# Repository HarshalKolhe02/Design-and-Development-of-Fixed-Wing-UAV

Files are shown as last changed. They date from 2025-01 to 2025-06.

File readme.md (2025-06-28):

# DESIGN AND DEVELOPMENT OF FIXED WING UAV
This is official repository of design and development of fixed wing UAV project at IvLabs, VNIT Nagpur
#
<details>
  <summary>Table of Content</summary>
  <ol>
    <li><a href="#DESIGN METHODOGOLGY">Design Methodology</a></li>
   <ol>
     <li><a href="#AIRFOIL SELECTION">Airfoil Selection</a></li>
     <li><a href="#WEIGHT ESTIMATION">Weight Estimation</a></li>
     <li><a href="#Thrust To Weight Ratio">Thrust To Weight Ratio</a></li>
     <li><a href="#Configuration of Aircraft">Configuration of Aircraft</a></li>
     <li><a href="#Estimation and Adjustment">CoG Estimation and Adjustment</a></li>
     <li><a href="#Demensions of Aircraft">Demensions of Aircraft</a></li>
   </ol>   
    <li><a href="#Fabrication">Fabrication</a></li>
     <li><a href=""#Flight Test"">Flight Test</a></li>
  </ol>
</details>

## DESIGN METHODOGOLGY
### AIRFOIL SELECTION
Airfoil selection is done by selecting different airfoils and then analysing them using XFLR5. We found that NACA2412 with camber 4%  gives us $C_l=1$ at 4 $^\circ$ -5 $^\circ$ AOA. The simulation graphs are shown below.

simulation sheet

We have designed rectangular wing using this airfoil and elevator, rudder are kept Flat.

### WEIGHT ESTIMATION
For estimation of weight, we have found weight of each component individually and then added to get final weight of plane. 
The estimated weight was found to be 1580 grams. The actual weight of plane (as of now) is 1350 grams.
### WING SPAN CALCULATION
For the calculation of wing span We have taken aspect ratio to be 5 which is common for trainers UAV. Then by using the relation of wing loading we found that the wing area to be 3125 $cm^2$ 
By using the aspect ratio relation we found the length of wing to be 1.25m and  chord length of 25 cm.

### THRUST TO WEIGHT RATIO
Generally the thrust to weight ratio for a fixed wing plane is kept between $0.5$ to $0.7$ . For this plane we have consider the thrust to weight ratio to be $0.5$ . A thrust-to-weight ratio (TWR) of 0.5 means that the thrust generated by the propulsion system is half the weight of the aircraft.
### CONFIGURATION OF AIRCRAFT
Considering the easy of manufacturing, We have considered the following configuration parameters for the plane
1. High wing configuration with no dihedral
2. Rectangular wing design
3. Tractor configuration
### CoG ESTIMATION AND ADJUSTMENT
The estimation of centre of gravity is done manually using the fact that the weight of the plane is balanced on the centre of gravity. For adjustment of CoG we adjusted the position of the battery to get the Cog behind the aerodynamic centre of plane i.e $\frac{MAC}{4}$.
### Landing gears
We have used a  taildragger configuration of landing gear. The back landing gear is smaller allowing plane’s wing to get required angle of attack during takeoff.
### DIMENSIONS OF AIRCRAFT 
The dimensions of aircraft are calculated using the standard equations of Fixed Wing Aeroplanes and are verified using the calculator Provided by rcplanes.online . 

A CAD model of aircraft is prepared using this dimensions and fabrication is made with refrence to CAD model.

### CAD MODEL

plane alternate

## 
## FABRICATION

The fuselag of plane is made using foam sheet cutted into various pieces and then glued together. The wings are made by using styrofoam blocks from which airfoils are made using hot wire cutter in various parts all these parts are combined using Carbon Fibre Rod. The Elevator, Ailerons and Rudder are made using foam sheet. Servos are used to move the control surfaces. The mount for motor, servo connections and landing gears are 3d printed. The Final Fabricated Plane is shown below.

Final_plane)
##

## FLIGHT TEST

[FLIGHT TEST](https://github.com/user-attachments/assets/4fe1304d-87b4-4691-89f3-da415da7d665)

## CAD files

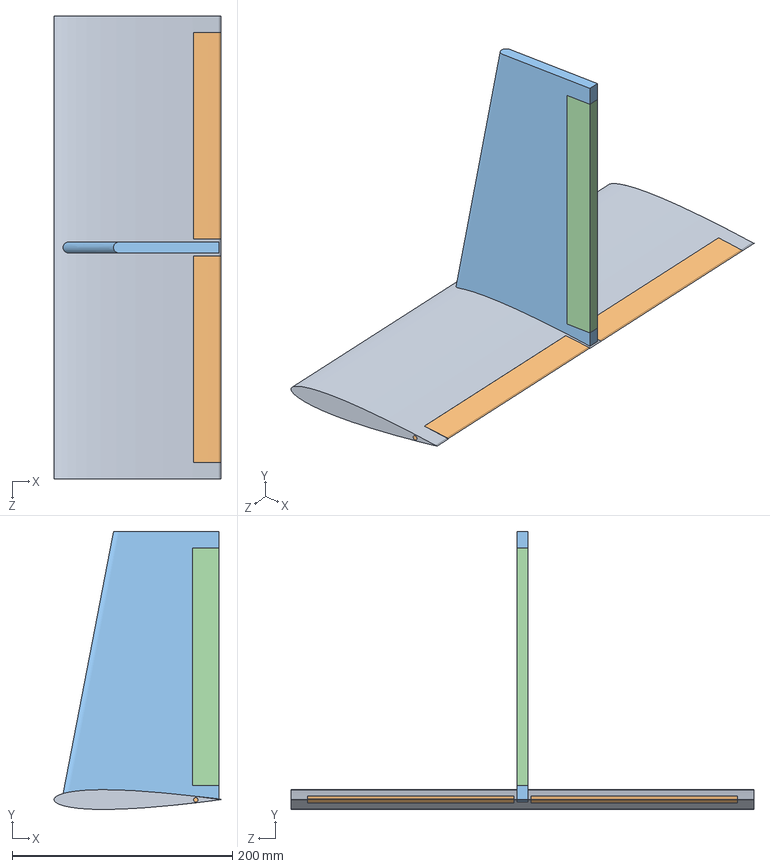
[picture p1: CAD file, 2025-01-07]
CAD files/HS_final.SLDASM
151.3 x 252.2 x 420.0 mm
HS
Part2^HS_final x 2
fin
Part3^Tail_final

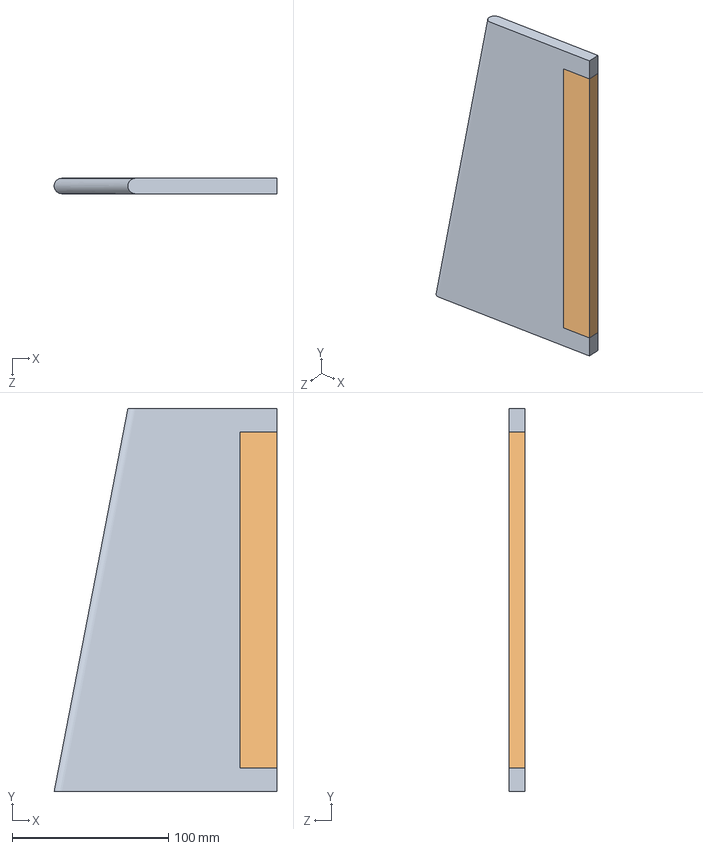
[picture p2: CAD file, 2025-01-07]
CAD files/Tail_final.SLDASM
142.7 x 245.4 x 10.0 mm
fin
Part3^Tail_final

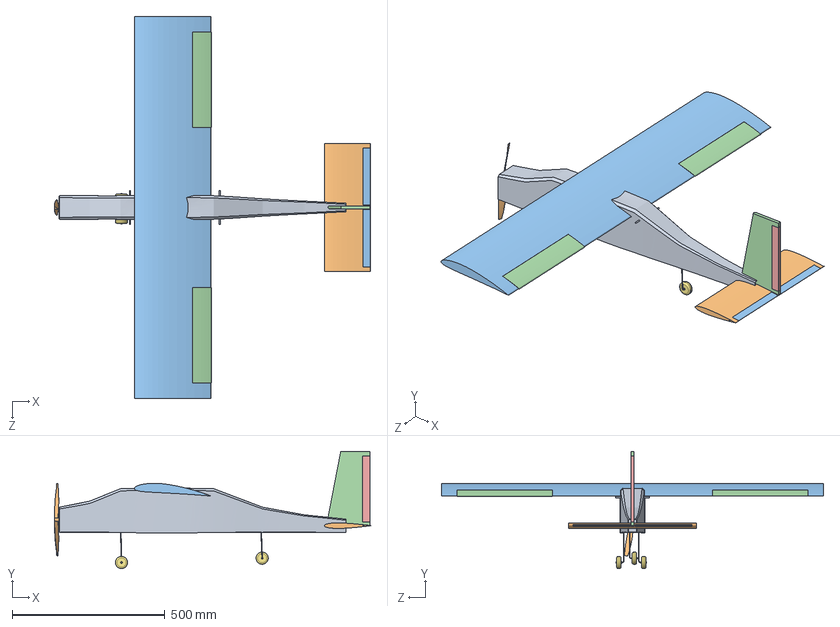
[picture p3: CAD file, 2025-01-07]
CAD files/plane alternate.SLDASM
1034.2 x 383.8 x 1250.0 mm
fuselagalternate
HS
Part2^HS_final x 2
fin
Part3^Tail_final
motor_mount
wheel x 3
fwg
bwg
prop
wing2412
aelioron x 2

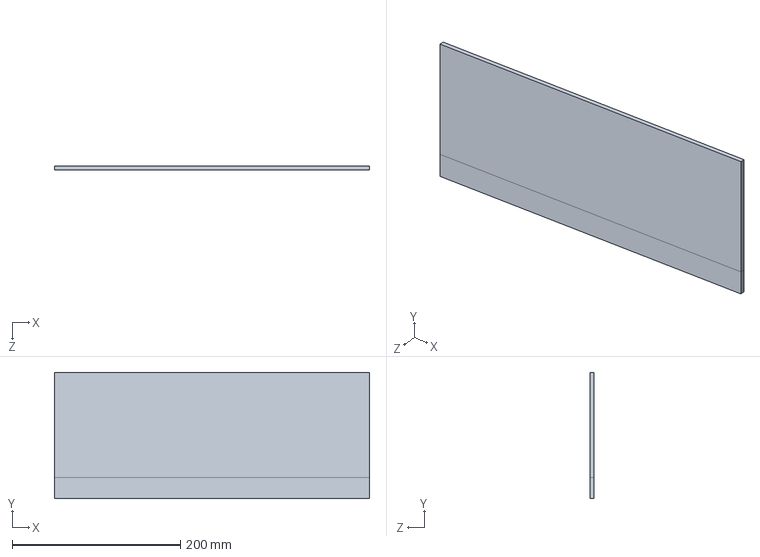
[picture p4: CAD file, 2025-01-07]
CAD files/elevator.SLDPRT
375.0 x 150.0 x 5.00 mm

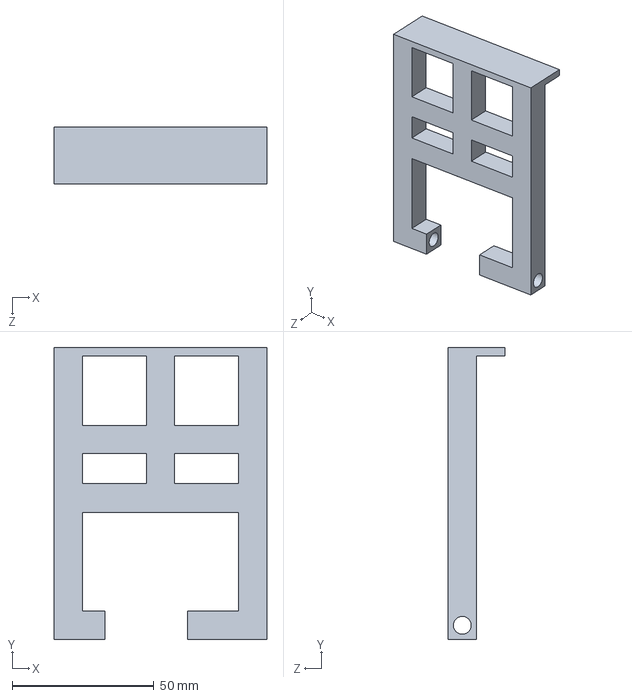
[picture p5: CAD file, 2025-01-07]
CAD files/wheelbaseback.SLDPRT
75.0 x 103.0 x 20.0 mm

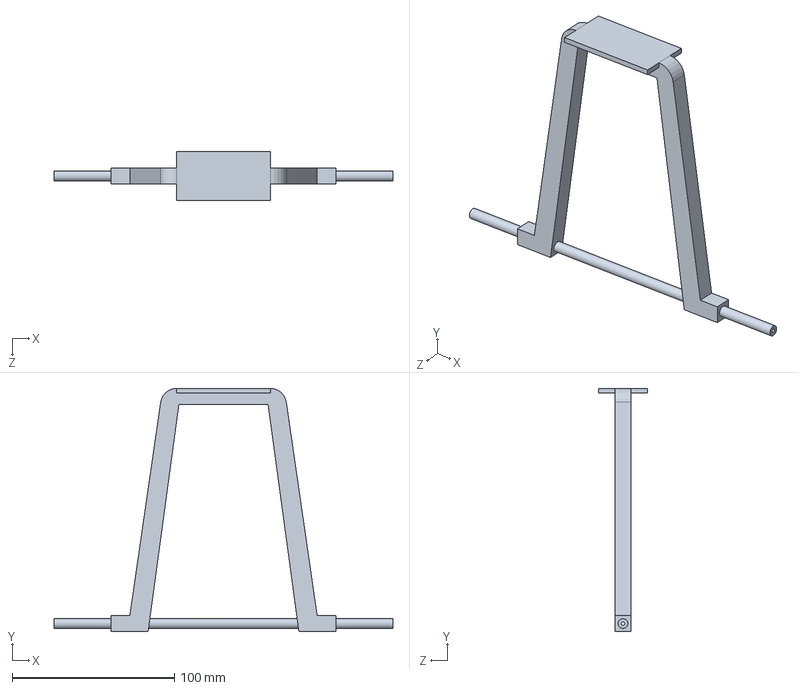
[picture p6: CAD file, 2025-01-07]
CAD files/wheelbase.SLDPRT
209.0 x 150.0 x 30.0 mm

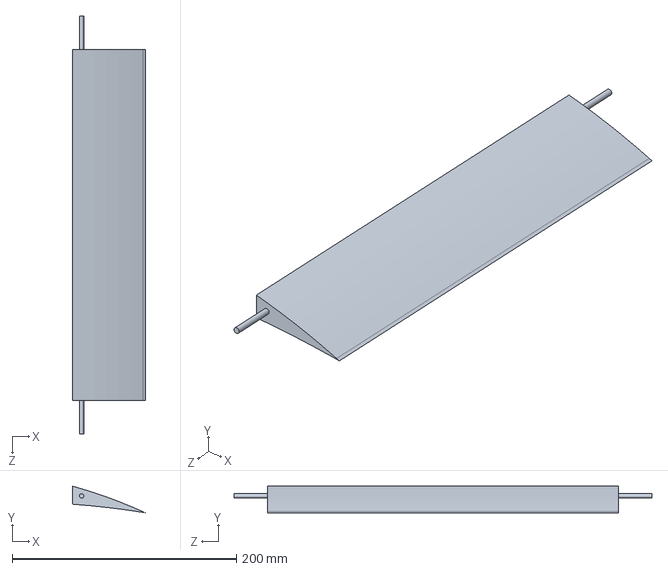
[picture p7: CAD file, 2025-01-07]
CAD files/aelioron.SLDPRT
64.8 x 23.7 x 372.5 mm

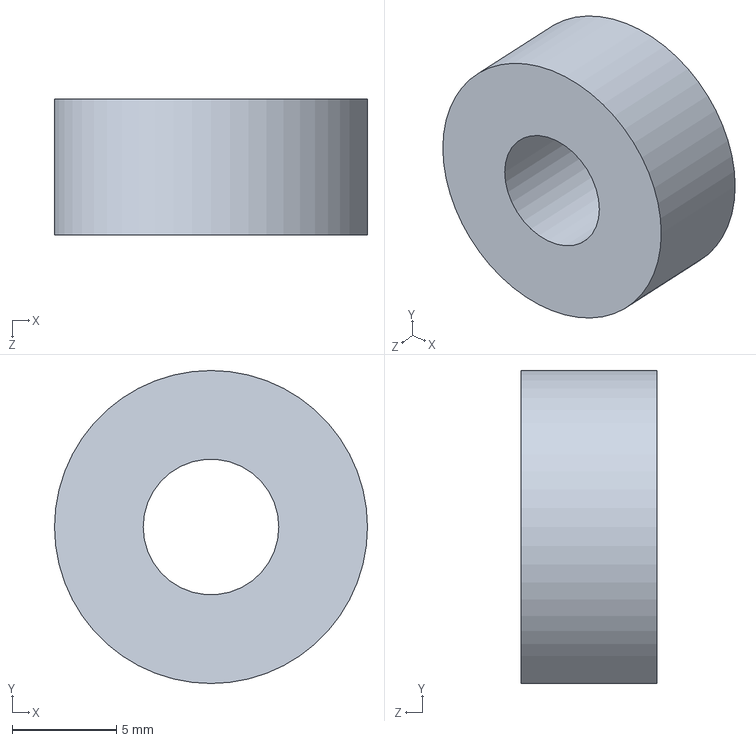
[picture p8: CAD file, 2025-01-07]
CAD files/wheel_lock.SLDPRT
15.0 x 15.0 x 6.50 mm

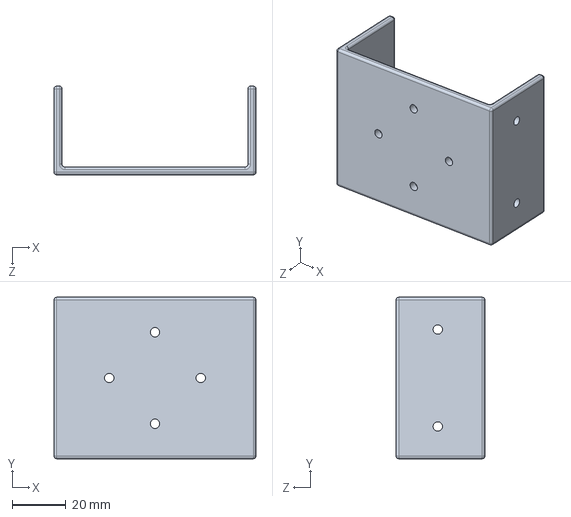
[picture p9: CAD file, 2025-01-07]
CAD files/motor_mount_new.SLDPRT
75.0 x 60.0 x 33.0 mm

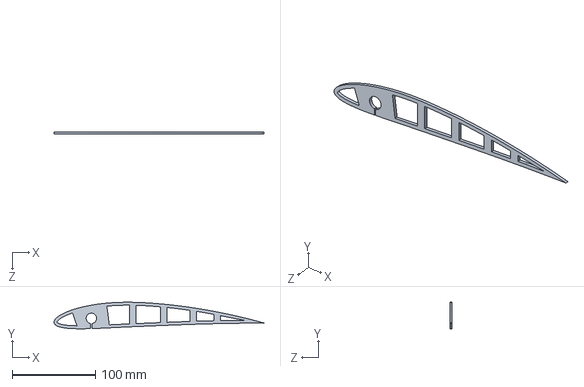
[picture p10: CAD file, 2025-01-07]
CAD files/airfoil right.SLDPRT
252.3 x 32.0 x 3.00 mm

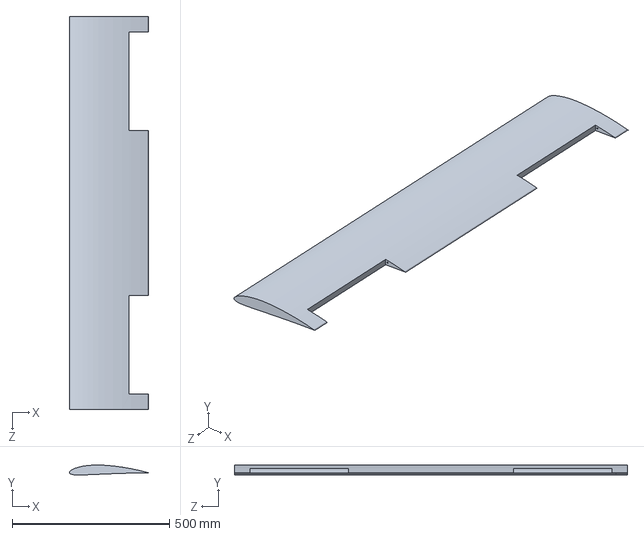
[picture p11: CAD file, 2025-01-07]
CAD files/wing2412.SLDPRT
252.3 x 31.9 x 1250.0 mm

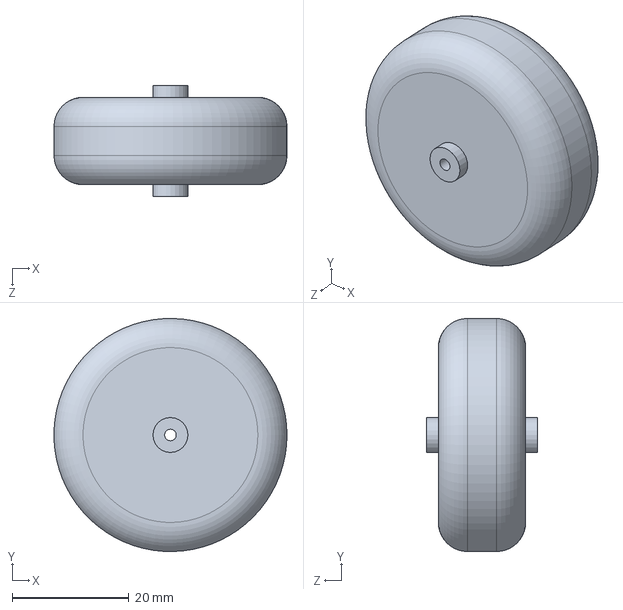
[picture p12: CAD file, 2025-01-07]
CAD files/wheel.SLDPRT
40.0 x 40.0 x 19.0 mm

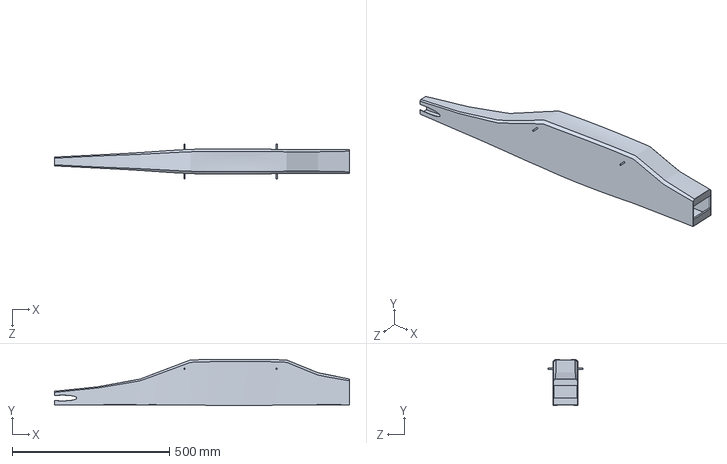
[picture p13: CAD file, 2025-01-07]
CAD files/fuselagalternate.SLDPRT
937.8 x 147.4 x 110.0 mm

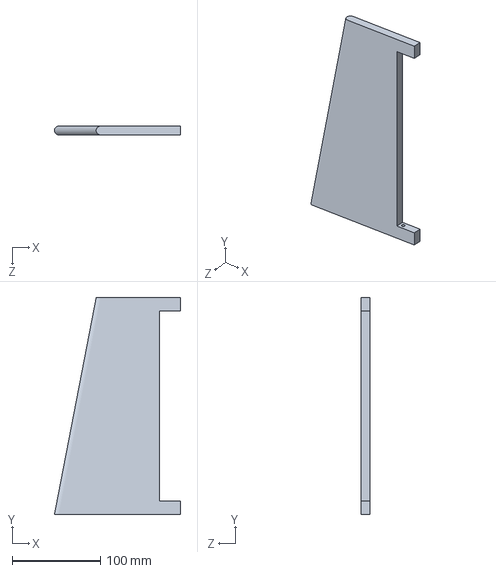
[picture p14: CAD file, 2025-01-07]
CAD files/fin.SLDPRT
142.7 x 245.4 x 10.0 mm

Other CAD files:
CAD files/Lmount.SLDPRT
